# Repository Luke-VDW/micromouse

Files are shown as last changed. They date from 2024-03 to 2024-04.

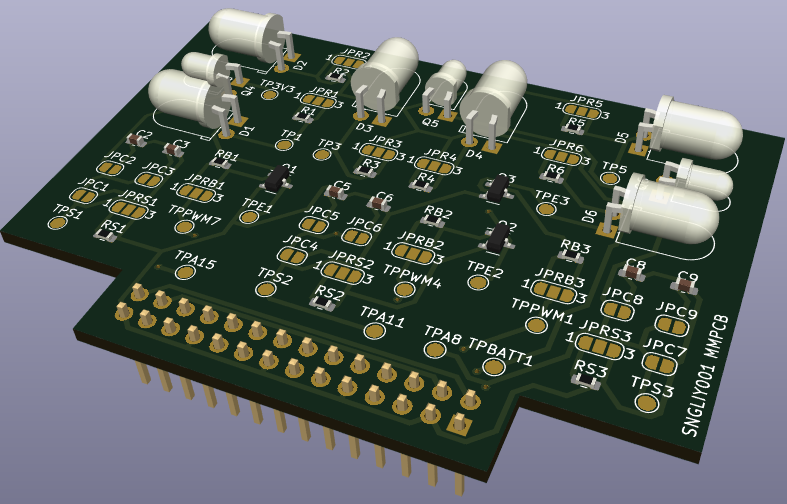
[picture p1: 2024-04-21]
documents/sensing/diagrams/PCB3D.png

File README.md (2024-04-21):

# micromouse
This repository contains all documentation used and deliverables produced for the UCT EEE3088F micromouse project.

A micromouse is a battery powered robot whose goal is to navigate through a maze. The project focuses on the design of the micro-mouse’s hardware. The project is compartmentalised into four subsystems, namely: the motherboard, the processor, power and sensing. The processor subsystem and motherboard subsystem have been completed. This repository will contain the power subsystem and sensing subsystem documentation.

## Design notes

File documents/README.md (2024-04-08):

This folder contains documentation relevant to both the power and sensing subsystem of the micromouse.

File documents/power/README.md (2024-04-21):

This folder contains documentation for the power subsystem within the context of the UCT EEE3088F Micro-mouse project. The power subsystem is one of four subsystems in this project, namely: the motherboard, the processor, power and sensing.

The documentation is for the design and manufacturing of the power subsystem that is responsible for powering the other subsystems.

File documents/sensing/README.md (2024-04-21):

This folder contains documentation for the sensing subsystem within the context of the UCT EEE3088F Micro-mouse project. The sensing subsystem is one of four subsystems in this project, namely: the motherboard, the processor, power and sensing.

The documentation is for the design and development of the sensing PCB responsible for detecting obstructions(walls) nearby and providing the processor with that data.

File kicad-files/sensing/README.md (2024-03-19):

This folder contains all kicad material for the sensing subsystem of the micromouse project.

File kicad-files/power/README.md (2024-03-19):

This folder contains all kicad material for the power subsystem of the micromouse project.

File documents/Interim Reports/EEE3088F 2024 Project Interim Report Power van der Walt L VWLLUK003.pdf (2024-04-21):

# Interim Design Report

Micromouse Power Subsystem


Prepared by:
Luke van der Walt

Prepared for:
EEE3088F
Department of Electrical Engineering University of Cape Town

April 21, 2024

# Declaration

1. I know that plagiarism is wrong. Plagiarism is to use another’s work and pretend that it is one’s own.
2. I have used the IEEE convention for citation and referencing. Each contribution to, and quotation in, this report from the work(s) of other people has been attributed, and has been cited and

referenced.

3. This report is my own work.
4. I have not allowed, and will not allow, anyone to copy my work with the intention of passing it off as their own work or part thereof.

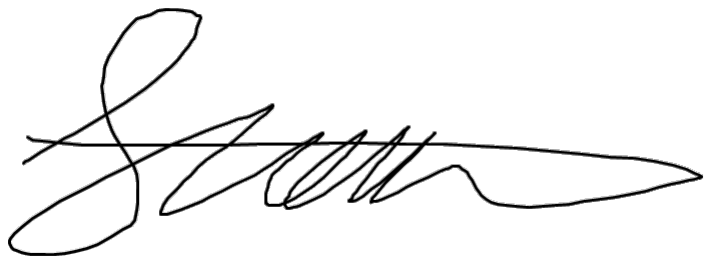
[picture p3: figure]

April 21, 2024

Name Surname | Date

ii

# Contents

1 Introduction | 1
2 Requirements Analysis | 2
3 Subsystem Design | 5
4 Acceptance Testing | 12

iii

# Chapter 1

# Introduction

## 1.1 Problem Description

This project encompasses the development of a power module and it was assigned as part of the EEE3088F course offered by the EBE faculty at the University of Cape Town. It exists under a larger project aimed at developing a micromouse robot. A micromouse is a battery-powered, wheeled robot whose goal is to traverse and solve a maze. In this micromouse project, the robot will navigate through a walled maze structure and attempt to reach its center. The micromouse project is structured around four distinct yet interconnected subsystems namely: the motherboard, processing, power, and sensing subsystems.

This specific project focuses on the power subsystem. The power subsystem needs to provide power from a battery to the motors and it needs to be able to charge the battery. Additionally, it must interface appropriately with the other three subsystems and provide them access to the battery.

## 1.2 Scope and Limitations

This project’s scope covers the design, manufacturing, and hardware testing of the power subsystem for the micromouse project. The developed module only needs to meet the requirements detailed in section 2.1. Note this project does not cover the development of the other three subsystems; this includes any programmed communication or inputs to the power subsystem from other subsystems. Additionally, the physical assembly of this module is done by a third party and lies outside the scope of this project.

This project was limited to a fixed budget of $8.25 and a design completion deadline of 24 March 2024.

Additionally, the design was limited by the following:

- The module with all its components had to be manufactured through JLCPCB.
- The module size and interfacing capabilities were limited by the motherboard subsystem.
- The module could only be tested through simulations or calculations before manufacturing.
- The power supplied was limited to a single 1S1P LiPo battery.

## 1.3 GitHub Link

All relevant information and documentation can be found in the following GitHub repository: https://github.com/Luke-VDW/micromouse/tree/main.

# Chapter 2

# Requirements Analysis

## 2.1 Requirements

The requirements for a micromouse power module are described in Table 2.1.

Table 2.1: User and functional requirements of the power subsystem.

Requirement ID | Description
R01 | Must operate off a single 1S1P LiPo battery
R02 | Must be able to charge the battery from a 5V pin
R03 | Must provide sufficient power to the DC brush motors and other subsystems
R04 | Must enable speed and direction control for the motors
R05 | Must be able to switch the micromouse ON / OFF
R06 | Must charge the battery when the micromouse is off
R07 | Must provide an analogue battery state of charge signal out
R08 | Must cost within the budget
R09 | Must be manufactured with all its components through JLCPCB
R10 | Must fit on a PCB that can connect to the motherboard

## 2.2 Specifications

The specifications, refined from the requirements in Table 2.1, for the micromouse power module are described in Table 2.2.

Table 2.2: Specifications of the power subsystem derived from the requirements in Table 2.1.

Specification ID | Description
SP01 | The battery must connect to the board via a JST PH 2mm connector
SP02 | The module must operate from 3.0 - 4.2V
SP03 | The battery charging input must not exceed 4.2V
SP04 | The battery must be charged at a rate less than 800mA (1C)
SP05 | The motors must each be able to receive up to 200mA of continuous current
SP06 | The module must supply the other subsystems with power at their peak load
SP07 | The motors’ speed and direction must be controlled using 3.3V PWM signals
SP08 | The module must provide 0V or 3.0 - 4.2V to the motors and other subsystems
SP09 | When the micromouse is OFF the battery must draw below 500uA
SP10 | When the micromouse is OFF the charging circuitry must still connect to the battery
SP11 | The SoC output must be less than 3.3V
SP12 | The module must cost less than $8.25
SP13 | The components chosen for the module must be sufficiently stocked at JLCPCB
SP14 | The board must be smaller than 100x100mm
SP15 | Must have a 2x8 2.54mm pin pitch header to connect to the motherboard
SP16 | The header must be centred in a tab with a minimum height of 18mm and a maximum width of 35mm

2.3. Testing Procedures

## 2.3 Testing Procedures

A summary of the testing procedures detailed in chapter 4 is given in Table 2.3.

Table 2.3: Testing procedures of the power subsystem derived from the specifications in Table 2.2

Acceptance Test ID | Description
AT01 | Check the module turns on
AT02 | Measure the input battery voltage
AT03 | Measure battery input current
AT04 | Measure the current going into the motors
AT05 | Measure the current going to the other subsystems
AT06 | Measure the frequency and direction of the motor output voltage
AT07 | Measure the voltage output to the motors and subsystems when switched off
AT08 | Measure the current going to the entire micromouse
AT09 | Measure the SoC voltage output
AT10 | Use JLCPCB to check prices and stock levels
AT11 | Measure the module’s physical dimensions
AT12 | Check the module can connect to the motherboard using the header

## 2.4 Traceability Analysis

The show how the requirements, specifications and testing procedures all link, Table 2.4 is provided.

Table 2.4: Requirements Traceability Matrix

# | Requirements | Specifications | Acceptance Test

1 2 3 4 5 6 7 8 9 10 | R01 R02 R03 R04 R05 R06 R07 R08 R09 R10 | SP01,SP02 SP03,SP04 SP05,SP06 SP07 SP08,SP09 SP10 SP11 SP12 SP13 SP14,SP15,SP16 | AT01 AT02,AT03 AT04,AT05 AT06 AT07,AT08 AT02,AT03,AT07 AT09 AT10 AT10 AT11,AT12

### 2.4.1 Traceability Analysis 1

From R01, SP01 and SP02 can be deduced because the battery being used has a JST PH 2mm connector, and the module must operate at the supplied battery voltage which ranges from 3.0V -4.2V. This can be tested with AT01 to see if the module turns on.

### 2.4.2 Traceability Analysis 2

From R02, SP03 and SP04 can be deduced because the battery has a maximum voltage of 4.2V and a maximum rated charge current of 800mA (1C). These can be tested with AT02 and AT03 by measuring

the voltage across and the current flowing into the battery.

2.4. Traceability Analysis

### 2.4.3 Traceability Analysis 3

From R03, SP05 and SP06 can be deduced because the module should allow the motor to operate at the maximum current they can draw at the rated voltage of the battery, which is 200mA. The module should also be capable of transferring power to the other subsystems at their peak loads. This can be tested with AT04 and AT05 to check that the module can transfer enough power.

### 2.4.4 Traceability Analysis 4

From R04, SP07 can be deduced because the module only has access to 2 PWM signals for motor control and these come from the STM32 processor which outputs 3.3V logic signals. This can be tested with AT06 to ensure that the module will output the correct response from a set of PWM inputs.

### 2.4.5 Traceability Analysis 5

From R05, SP08 and SP09 can be deduced because when the micromouse is considered switched off the output voltage from the module must be 0V the battery current must be below 500uA; when switched on the output voltage must be between 3.0-4.2V and adhere to SP05. This can be tested with AT07 and AT08 by measuring the output voltage and battery current when it is switched on or off.

### 2.4.6 Traceability Analysis 6

From R06, SP10 can be deduced because the charging circuit must always be connected to the battery so it can charge when the micromouse is switched off. This can be tested with AT02, AT03 and AT07 to check that at 0V output voltage, the battery is charging at its rated values.

### 2.4.7 Traceability Analysis 7

From R07, SP11 can be deduced because the output of the analogue battery state of charge signal goes to an ADC input on the STM32L4 processor, which has a maximum rated reading input voltage of 3.3V. This can be tested with AT09 to ensure it is below 3.3V.

### 2.4.8 Traceability Analysis 8

From R08, SP12 can be deduced because this project has a budget of $8.25. This can be tested with

AT10 to check the total board price.

### 2.4.9 Traceability Analysis 9

From R09, SP13 can be deduced because all manufacturing done and components used in this project are limited to what is offered on JLCPCB. This can be tested with AT10 to check that the components used are available at JLCPCB.

### 2.4.10 Traceability Analysis 10

From R10, SP14, SP15, and SP16 can be deduced because the module must be able to connect with the motherboard through a 2x18 pin connector and because the size of the module is limited by the motherboard. This can be tested with AT11 and AT12 to check that the board fits onto the motherboard.

# Chapter 3

# Subsystem Design

## 3.1 Design Decisions

The power module was broken up into 4 main sections for the sake of the design decisions. These sections are the charging, driver, SoC and PCB design sections as seen in Figure 3.1.

Figure 3.1: Section diagram for the power module

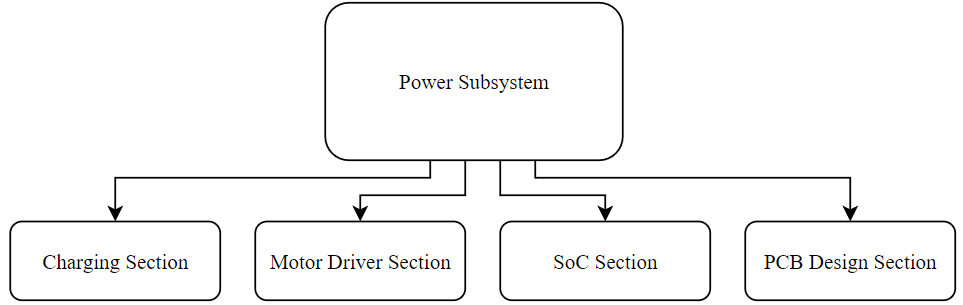
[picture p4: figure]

### 3.1.1 Charging Section

The charging section for the battery must meet requirements: R02, R06, R08 and R09 listed in Table 2.1. Therefore the circuit must comply with specifications: SP03, SP04, SP09, SP10, SP12, and SP13 listed in Table 2.2.

Considerations to take into account when meeting the requirements include:

- The solution should be very reliable since improperly charging the battery is a fire hazard
- The solution should draw below 500uA when it is not charging because it will remain connected to the micromouse when it is switched off
- The battery charging current should be optional to allow for different charging currents
- The battery should not take excessively long to charge

Possible design solutions can be seen in Table 3.1.

Table 3.1: Possible design solutions for the charging section

Design Solution ID | Possible Design Solution
DS01 | Use a custom charging circuit with auto-cutoff and current limiting
DS02 | Use a LiPo charging IC available

Chosen solution: DS02

A custom charging circuit would provide and more modifiable circuit than using an IC however it is much more complicated and is less safe than a dedicated LiPo charging IC. Additionally, a charging IC will likely be more efficient than a custom circuit and come with documentation to support all its parameters, hence it is the preferred solution.

Some available battery management ICs that satisfy the charging requirements can be seen in Table 3.2 below:

3.1. Design Decisions

Table 3.2: Component considerations for the charging section

Component | Price ($) | Stock | Basic part | Adjustable current | Max current (A)
TP4056-42 | 0.1724 | 107303 | Yes | Yes | 1
GX4057 | 0.0189 | 14048 | Yes | No | 0.5
TP4057-42 | 0.1163 | 21877 | Yes | Yes | 0.5

Chosen component: TP4056-42 (https://dlnmh9ip6v2uc.cloudfront.net/datasheets/Prototyping/TP4056.pdf)

The GX4057 is much cheaper than the other options, however since it is not a basic part it will have an extended component fee of $2.87 and hence is significantly more expensive than the other options.

The TP4057-42 is cheaper than the TP4056-42 however its charging current is limited to 500mA and it is less available, which makes the TP4056-42 the preferred component.

Calculations for the TP4056-42:

The charging current is given as IBAT =

| | | 1 RP ROG
× 1200 where RP ROG is a resistor connected to the PROG pin (pin 2) and ground.

The maximum charging current for the battery is 800mA and the recommended is 400mA. Any charging current between these values will be fast enough and safe. The associate resistor values are:

| 0.8 = | 1

RP ROGmax

| | | × 1200 | ∴ RP ROGmax = 3kΩ
| 0.4 = | 1

RP ROGrec

| | | × 1200 | ∴ RP ROGrec = 1.5kΩ

The STDBY and CHRG pins (pins 6 and 7) can be connected to a green and red LED respectively.

These are used to indicate when the unit is charging. A 1kΩ resistor can be placed in series with the LED to limit the current through them.

As recommended by the datasheet a 10µF capacitor can be connected across VCC and ground and across the BAT pin and ground. Additionally, a limiting resistor should be connected in series with VCC that can range between 0.2Ω - 0.5Ω. The max power that could be dissipated across this resistor is P = I

2 × R = 0.8

2 × 0.5 = 0.32W. Therefore use two or more 250mW 1Ω resistors in parallel to

achieve this limiting resistance.

### 3.1.2 Motor Driver Section

The motor driver section must meet requirements: R01, R03, R04, R08 and R09 listed in Table 2.1. Therefore the circuit must comply with specifications: SP02, SP05, SP07, SP08, SP12 and SP13 listed in Table 2.2.

Considerations to take into account when meeting the requirements include:

- The solution should be capable of running at high PWM frequencies to provide a broad range for user selection

3.1. Design Decisions
- The output impedance for the incoming PWM signals should be kept high since this signal is a logic signal coming from the processor and is not meant to deliver power
- If a motor is connected across the battery directly, its voltage will decrease over time which will affect the motor’s speed

Possible design solutions can be seen in Table 3.3:

Table 3.3: Possible design solutions for the charging section

Design Solution ID | Possible Design Solution
DS03A | Use a custom H-bridge circuit powered directly from the battery
DS03B | Use a custom H-bridge circuit powered by a regulated voltage
DS04A | Use a motor driver IC powered directly from the battery
DS04B | Use a motor driver IC powered by a regulated voltage

Chosen solution: DS04A

A custom H-bridge circuit would provide a more modifiable circuit than using an IC however it is much more complicated and could potentially be less reliable than a driver IC. Operating at a constant voltage would provide stability on the output but it would also require a voltage regulator which would decrease the overall efficiency. The loss in efficiency is more important than the improved stability since the output can be controlled with a PWM input, which can be used to compensate for the changing battery voltage, and hence solution DS04A is the preferred solution.

Some available motor driver ICs that satisfy the motor driver requirements can be seen in Table 3.4:

Table 3.4: Component considerations for the charging section

Component | Price ($) Stock | Basic
part

No. of
drivers

Max
current (A)

Operating
voltage (V)
DRV8833PWPR | 0.6660 | 9436 | No | 2 | 1.5 | 2.7 - 10.8
DRV8837DSGR | 0.1235 | 71521 | No | 1 | 1.8 | 1.8 - 7.0

Chosen component: DRV8833PWPR (https://wmsc.lcsc.com/wmsc/upload/file/pdf/v2/lcsc/1810151712_Texas-Instruments-DRV8833PWPR_C50506.pdf)

The DRV8837DSGR and the DRV8833PWPR can both meet the requirements for the driver circuit, however, the DRV8833PWPR is a dual driver and can therefore operate both motors at the same time. Having one IC instead of two reduces the complexity of the module which is favoured over the small cost difference between the two and therefore the DRV8833PWPR is the preferred component.

Calculations for the DRV8833PWPR:

As recommended by the datasheet a 10µF ceramic capacitor can be connected across VM and ground and a 2.2µF ceramic capacitor can be connected across VINT and ground. Additionally, a 10nF ceramic capacitor can be connected across VM and VCP. AISEN and BISEN can be grounded to ignore current limits.

3.1. Design Decisions

### 3.1.3 SoC Section

The SoC section must meet requirements: R01, R07, R08 and R09 listed in Table 2.1. Therefore the circuit must comply with specifications: SP02, SP11, SP12, and SP13 listed in Table 2.2.

Considerations to take into account when meeting the requirements include:

- The voltage output should be a linearly scaled version of the input since this output signal will be used to determine the battery state of charge
- The output must be able to be polled by an ADC input without unwanted loading effects

Possible design solutions can be seen in Table 3.5.

Table 3.5: Possible design solutions for the SoC section

Design Solution ID | Possible Design Solution
DS05 | Use a voltage diver to scale the input and then output from an op-amp buffer
DS06 | Use a voltage diver to scale the input and then output after a capacitor acting as a buffer

Chosen solution: DS06

The op-amp buffer would be reliable and easy to implement however since we are operating at low voltages it would be easier to avoid using active components that can run into headroom issues. Therefore, since it is a passive solution, DS06 is the preferred solution.

Calculations for the SoC section:

The voltage divider input ranges from 3.0 - 4.2V. The output must be below 3.3V for the ADC to be able to properly read it therefore, so for the maximum VIN :

VOUT = VIN ×

R2
R1 + R2

∴ 3.3 = 4.2 ×

R2
R1 + R2

∴ R1 = R2 × 0.273

LetR2 = 10kΩ ∴ R1 = 2.73kΩ

Let R1 be a larger E24 value to ensure that the voltage is always lower than 3.3V, i.e. R1 = 3kΩ:

∴ VOUTmax = 4.2 ×

10k
3k + 10k

= 3.23V

The buffer capacitor for the output can be any size that is larger than the internal capacitor on the ADC of the processor.

3.1. Design Decisions

### 3.1.4 PCB Design Section

The PCB section must meet requirements: R03, R05, R08, R09 and R10 listed in Table 2.1. Therefore the circuit must comply with specifications: SP01, SP06, SP08, SP12, SP13, SP14, SP15 and SP16 listed in Table 2.2.

Considerations to take into account when meeting the requirements include:

- The switch should hold its position (latching) and should handle the peak current draw
- The PCB power traces should be able to handle the peak current draw of the micromouse
- The PCB should be as short as possible to help maintain a central centre of mass
- Power components should be as close together as possible to reduce the length of power traces

### 3.1.5 Final Design

The following design was chosen based on the design solutions DS02, DS04A and DS06 and any accompanying design considerations for each section above. The solution makes use of the TP4056-42 and the DRV8833PWPR as ICs for the charging and motor driver sections. For the charging circuit, five 1Ω are placed in parallel with jumpers to provide optional resistance values for the limiter resistor. Also, a parallel resistor loop controlled by a switch is connected alongside RP ROG to toggle the charging speed of the battery. The SoC section was designed with a range of buffer capacitor options. A large toggle switch was chosen to switch the micromouse on and off easily.

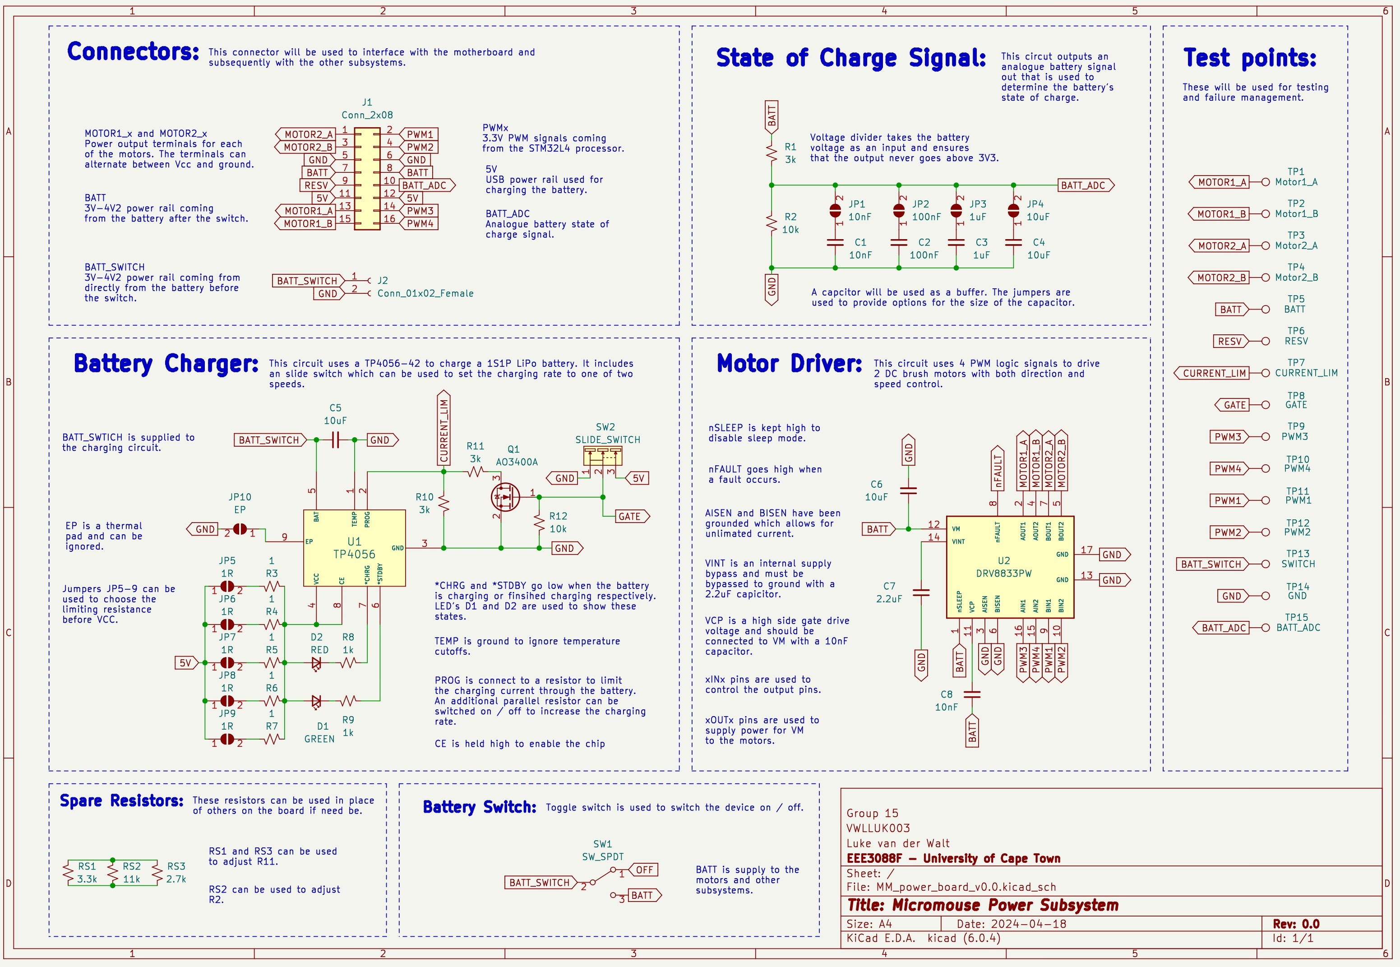
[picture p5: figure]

Figure 3.2: Final Schematic

3.2. Failure Management

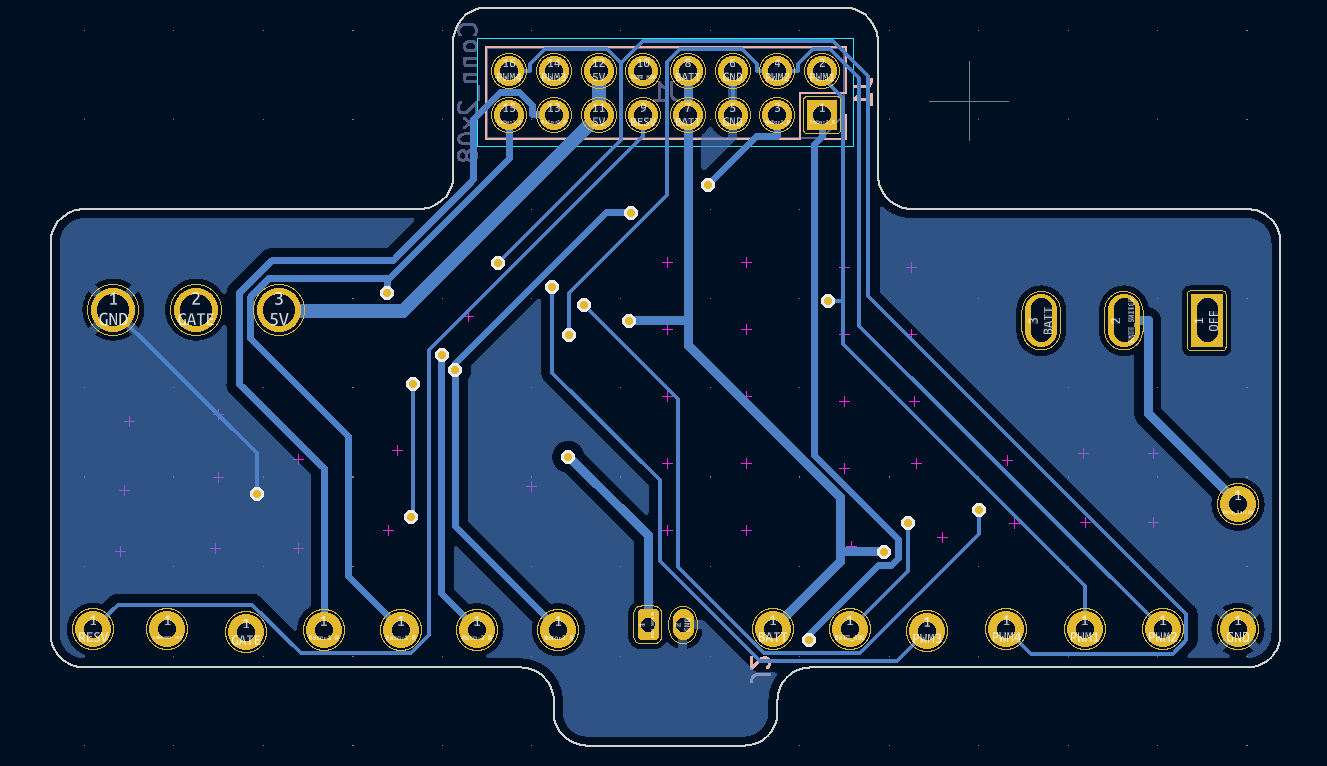
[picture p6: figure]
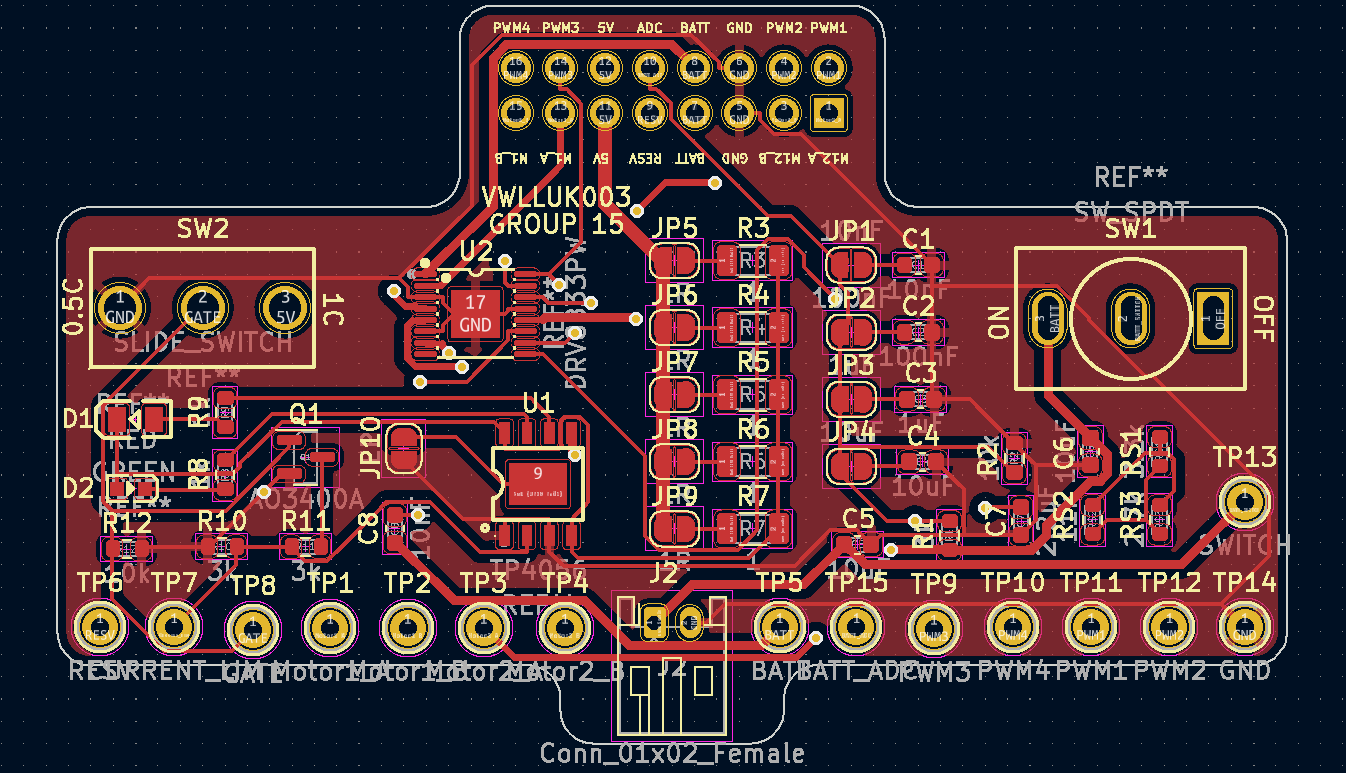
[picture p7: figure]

(a) Front PCB | (b) Back PCB

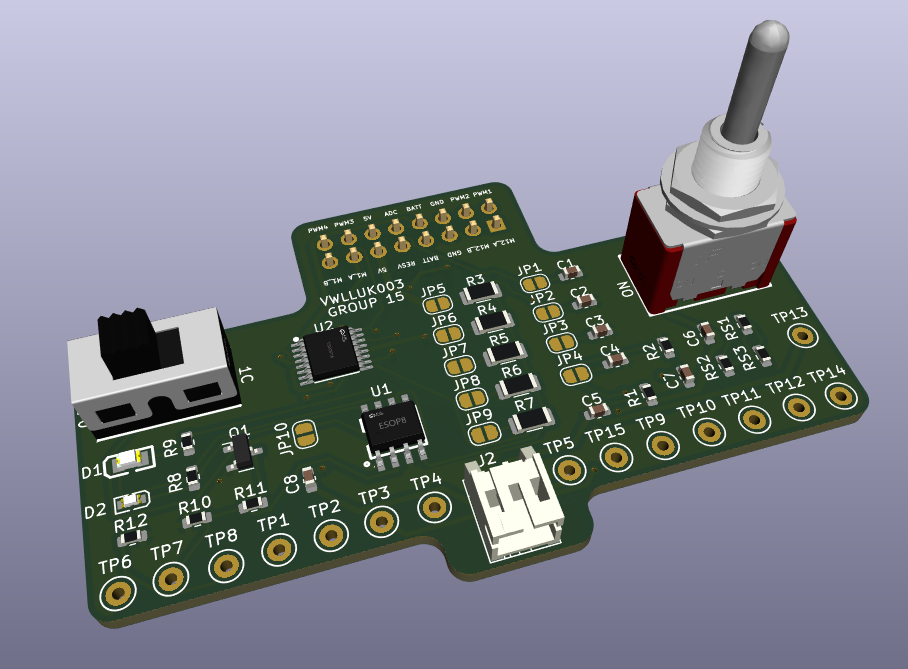
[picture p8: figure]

(c) 3D PCB

Figure 3.3: PCB

## 3.2 Failure Management

The steps taken to manage potential errors are detailed in Table 3.6.

Table 3.6: Failure management processes

Name | Description
Spare components | Spare resistors were added to the board. These resistors can be removed and placed elsewhere on the board if any other resistor values are off.
Jumpers | Jumpers have been placed in areas where the value of a component is uncertain to provide multiple options for that component.
TH test points | All test points are keystone / through hole which provides space to connect additional components in the event of a component failure.
Power test points | All power test points in the circuit have been connected using the same thick traces that the dedicated power lines use. This allows for power to be provided from these test points to other components through external connections if their traces have been incorrectly run.
Variable charging speed | A switch has been added to the charging circuit that allows for two different charging rates. If the set charging rate is too slow, this can be used to increase the charging rate, or it can be ignored if the rate is satisfactory.

3.3. System Integration and Interfacing

## 3.3 System Integration and Interfacing

Table 3.7: Interfacing specifications

Interface | Description | Pins/Output

PWM signals from STM
to power module through
header J1
- PWM1: STM PC6 to header PIN 2
- PWM2: STM PC7 to header PIN 4
- PWM3: STM PC8 to header PIN 14
- PWM4: STM PC9 to header PIN 16

Power from power module
to motors through header
J1
- MOTOR1_A: Header PIN 13 to Motor1 PIN A
- MOTOR1_B: Header PIN 15 to Motor1 PIN B
- MOTOR2_A: Header PIN 1 to Motor2 PIN A
- MOTOR2_B: Header PIN 3 to Motor2 PIN B
IJ1 | 3V - 4.2V power from the
power module to other subsystems through header J1
- BATT: Header PIN 7 and PIN 8 to STM VBAT
- GND: Header PIN 5 and PIN 6 to STM GND

5V power from USB to
power | module | through
header J1
- 5V: USB to header PIN 11 and PIN 12

Analogue SoC signal from
power module to STM
through header J1
- BATT_ADC: Header PIN 10 to STM 3V3 ADC
IJ2 | 3V - 4.2V power from battery to power module through JST connect J2
- BATT_SWITCH: + terminal to JST PIN 1
- GND: - terminal to JST PIN 2

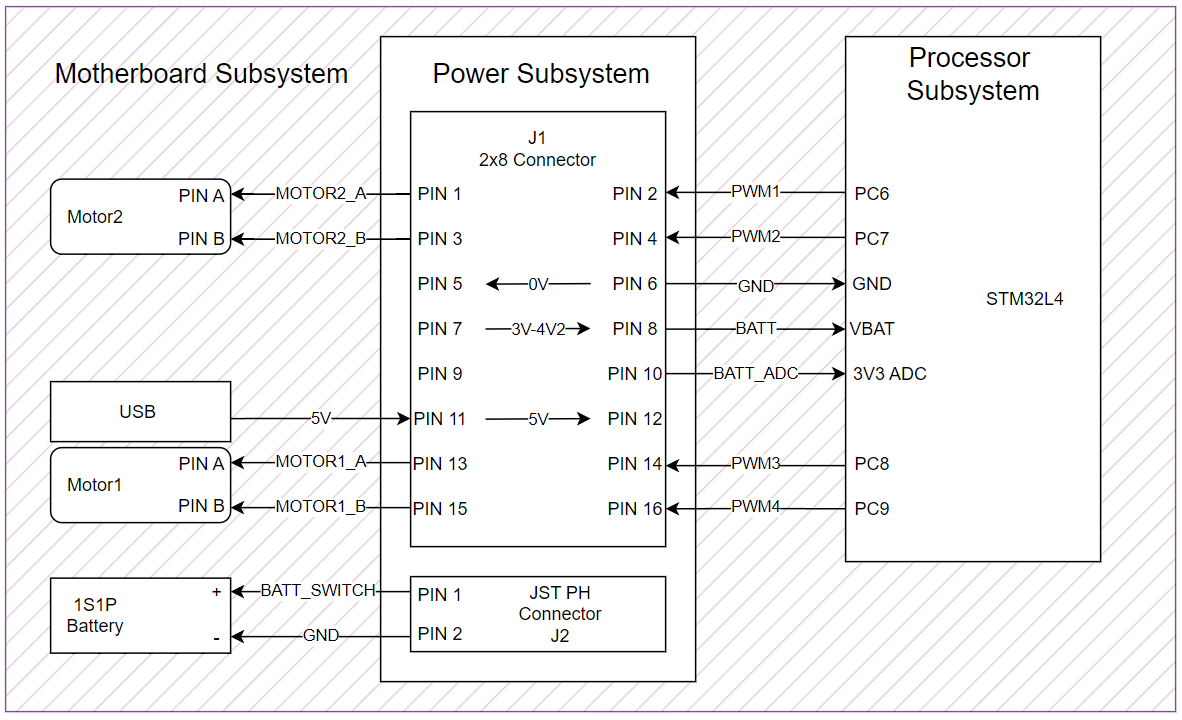
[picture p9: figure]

Figure 3.4: Interfacing Diagram

# Chapter 4

# Acceptance Testing

## 4.1 Tests

Table 4.1: Subsystem acceptance tests

Test
ID | Description | Testing Procedure | Pass Criteria
AT01 | Check the module
| turns on | • Connect the battery to the JST connector
| | • Measure the voltage on the PIN12 (VM) of U2 | 3V - 4V2
AT02 | Measure the input
| battery voltage | • Power the 5V pins on J1
| | • Measure the voltage across the terminals of J2
| | which is VBAT in | VBAT in ≈ 4V 2
AT03 | Measure battery input current
- Connect the positive terminal of an ammeter to
TP13 (BATT_SWITCH)
- Connect a semi-charged battery across the negative ammeter terminal and TP14 (GND)
- Power the 5V pins on J1
- Record IBAT T

IBAT T ≥ 0.4A
IBAT T ≤ 0.8A

AT04 Measure the cur- rent going into the motors
- Connect the positive terminal of an ammeter to TP1 (MOTOR1_A)
- Connect the negative terminal of the ammeter to pin A of Motor1 and PIN15 of J1 to pin B
- Connect a battery charged at 4V2
- apply a 3.3V DC signal to TP9 (PWM3) and connect TP10 (PWM4) to ground
- Repeat this for motors and record IM

IM > 0A
IM ≤ 0A2

AT05 Measure the cur- rent going to the other subsystemsConnect the positive terminal of an ammeter to TP5 (BATT)
- Connect the negative ammeter terminal to the BATT pin on the motherboard header
- Connect TP14 (GND) to the GND pin on the motherboard header
- Connect a charged battery to J2
•
- Record ISUB

ISUB ≤ 0A8

AT06 Measure the fre- quency and direc- tion of the motor output voltage

- Connect an oscilloscope to TP1 (MOTOR1_A)
- Record the fOUT and |VOUT |
- Repeat for TP3 (MOTOR2_A)

fOUT = fIN

Vout = Vbatt

4.1. Tests
AT07 | Measure | the
voltage output to
the motors and
subsystems when
| switched off
- Measure the voltage on TP5 (BATT)
- Record VBAT T

VBAT T = 0V

AT08 • Measure the cur- rent going to the entire micromouseConnect the positive terminal of an ammeter to TP13 (BATT_SWITCH)
- Connect a charged battery across the negative ammeter terminal and TP14 (GND)
- Connect header J1 to the motherboard
- Record Imm

Imm ≤ 0A8

AT09 Measure the SoC voltage output

- Measure the voltage on TP15 (BATT_ADC)
- Record VADC

VADC ≤ 3V 3

AT10 Use JLCPCB to check prices and stock levels taking
- Take note of basic vs extended parts
- Make a quote using the bill of materials and determine the total cost of the board
- Record Cost

Cost ≤ 8.25$

AT11 Measure the mod- ule’s physical di- mensions
- Use a measuring tool to measure the board’s total area A
- Use a measuring tool to measure the tab height

Htab
- Use a measuring tool to measure the tab width

Hwid

A ≤ 10 × 10cm
Htab ≥ 18mm
Hwid ≤ 35mm

AT12 Check the module can connect to
the motherboard
using the header
- Try to place the module header into the motherboard connector
- Once placed check that the module has access to the battery connector

Fits wihtout
obstruction

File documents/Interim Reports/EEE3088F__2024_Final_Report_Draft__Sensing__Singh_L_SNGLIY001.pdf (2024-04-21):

# Interim Design Report

Micromouse Sensing Subsystem


Prepared by:
Liyana Singh
SNGLIY001

Prepared for:
EEE3088F
Department of Electrical Engineering University of Cape Town

April 21, 2024

# Declaration

1. I know that plagiarism is wrong. Plagiarism is to use another’s work and pretend that it is one’s own.
2. I have used the IEEE convention for citation and referencing. Each contribution to, and quotation in, this report from the work(s) of other people has been attributed, and has been cited and referenced.
3. This report is my own work.
4. I have not allowed, and will not allow, anyone to copy my work with the intention of passing it off as their own work or part thereof.

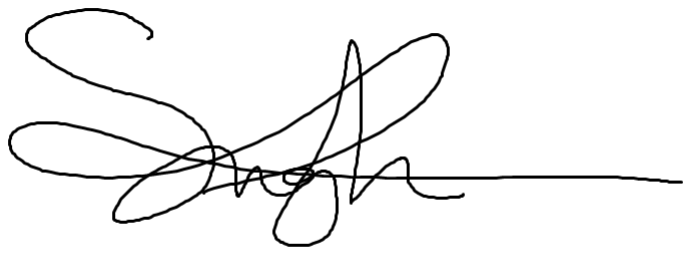
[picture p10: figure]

April 21, 2024

Name Surname | Date

ii

# Contents

1 Introduction | 1
2 Requirements Analysis | 2
3 Subsystem Design | 5
4 Acceptance Testing | 12

iii

# Chapter 1

# Introduction

### 1.1 Problem Description

### 1.1.1 Design Problem Statement

Design and develop a sensing PCB responsible for detecting obstructions(walls) nearby and providing the processor with that data.

### 1.1.2 Context

A micro-mouse is a battery powered robot whose goal is to navigate through a maze. This report is written on the sensing subsystem within the context of the UCT EEE3088F Micro-mouse project. The project focuses on the design of the micro-mouse’s hardware. The sensing subsystem is one of four subsystems in this project, namely: the motherboard, the processor, power and sensing.

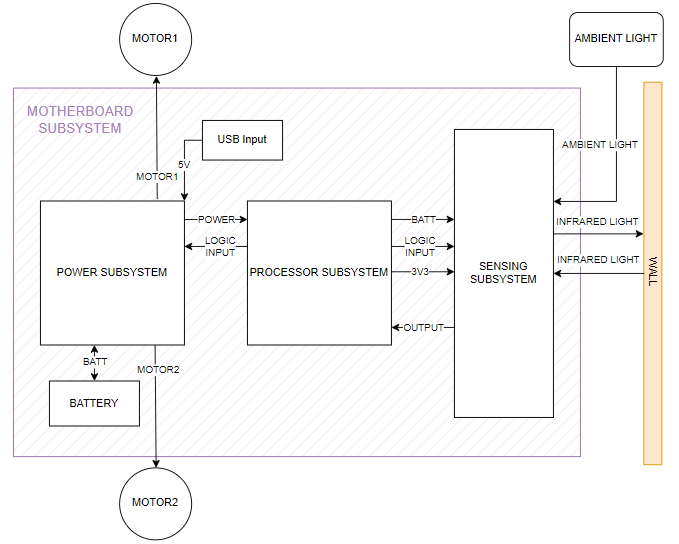
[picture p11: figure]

The motherboard connects all the subsystems. It
acts as a baseboard that the sensing subsystem slots
onto to connect to the processor subsystem. The power subsystem supplies the motherboard with power. The sensing subsystem is connected to the battery and 3.3V supply via the processor. The processor also supplies a logic input to the sensing subsystem. The sensing subsystem interacts with the environment to detect walls in the way of the micro-mouse. The sensing subsystem sends this data to the processor to be interpreted. This is summarised in Figure 1.1 adjacent. The power subsystem has been added for completeness but can be ignored.

Figure 1.1: Context Diagram

### 1.2 Scope and Limitations

The scope includes the design of the sensing PCB but the manufacturing of the PCB is external. It must detect walls, however, it does not have to interpret any data. The data is sent to the processor to be interpreted. It has design limitations: it must fit onto the pin headers on the motherboard, it must be an appropriate size for the micro-mouse and the components must be available on JLCPCB. Additionally, it has financial limitations: must not exceed $16.5 for two boards. Finally, it has a time limitation: must be completed by May 17th 2024.

### 1.3 GitHub Link

https://github.com/Luke-VDW/micromouse

# Chapter 2

# Requirements Analysis

### 2.1 Requirements

The requirements for a micro-mouse sensing module are described in Table 2.1.

Table 2.1: Requirements of the Sensing Subsystem.

Requirement ID | Description
R01 | It must be externally powered.
R02 | It must not exceed the power and current limitations.
R03 | It must detect walls.
R04 | It must prove it can detect walls
R05 | It must fit onto the pin headers on the motherboard.
R06 | It must be an appropriate size for the micro-mouse.
R07 | It must adhere to the budget.
R08 | All components must come from JLCPCB .

### 2.2 Specifications

The specifications, refined from the requirements in Table 2.1, for the micro-mouse sensing module are described in Table 2.2.

Table 2.2: Specifications of the Sensing Subsystem

Specification ID | Description
S01 | The IR emitter circuitry voltage will be supplied by the Battery LiPo 800mAh 3.7V.
S02 | The IR sensor circuitry voltage will be supplied by the 3.3V supply from the processor.
S03 | The maximum draw of 400mA from the battery results in a discharge time from full to fully discharged of 2 hours.
S04 | It must detect walls at the front, left and right sides of the PCB.
S05 | A simple code must be written to interpret the sensing subsystem’s output voltage that is sent to the processor.
S06 | The output voltage should be significantly greater than the minimum voltage output to indicate detection. The sensor detects ambient light and therefore the output voltage will have a non-zero minimum voltage output.
S07 | It must have a pin pitch less than or equal to 2.54mm.
S08 | The PCB’s size must not exceed an 80mm square.
S09 | The PCB component cost must not exceed $16.5 for 2 boards.
S10 | JLCPCB must have more than 1000 units available of the component.

2.3. Testing Procedures

### 2.3 Testing Procedures

A summary of the testing procedures detailed in chapter 4 is given in Table 2.3.

Table 2.3: Summary of Testing Procedures

Acceptance Test ID | Description
AT01 | Measure voltage across IR emitter circuitry.
AT02 | Measure voltage across IR sensor circuitry.
AT03 | Measure the current through the IR emitter circuit.
AT04 | Measure the current through the IR sensor circuit.
AT05 | Check there is IR emitter circuitry and IR sensor circuitry for the front, left and right sides of the PCB.
AT06 | The processor board has three LEDs. Observe LED1, LED2 and LED3 which indicate a wall is sensed on the left, front and right, respectively, by turning on. If no wall is sensed, then no LEDs will be on.
AT07 | Measure the output voltage of the IR sensor circuitry.
AT08 | Measure the pin pitch on the sensing PCB.
AT09 | Measure the PCB’s length and width.
AT10 | Check PCB cost is within budget.
AT11 | Check the manufacturing bill of materials.

### 2.4 Traceability Analysis

Table 2.4 shows how the requirements, specifications and testing procedures all link.

Table 2.4: Requirements Traceability Matrix

# | Requirements | Specifications | Acceptance Tests

1 | R01 | S01 S02 | AT01 AT02
2 | R02 | S03 | AT03 AT04
3 | R03 | S04 | AT05
4 | R04 | S05 S06 | AT06 AT07
5 | R05 | S06 | AT08
6 | R06 | S07 | AT09
7 | R07 | S08 | AT10
8 | R08 | S09 | AT11

### 2.4.1 Traceability Analysis 1

The sensing subsystem must be externally powered (R01). The voltage across the IR emitter circuitry (S01) will be measured (AT01) to test whether the voltage is within the battery’s range. Therefore, indicating whether it is successfully powered by the battery. The voltage across the IR sensor circuitry (S02) will be measured (AT02) to test whether the voltage is approximately 3.3V. Therefore, indicating whether it is successfully powered by the processor output.

2.4. Traceability Analysis

### 2.4.2 Traceability Analysis 2

The sensing subsystem must not exceed the power and current limitations(R02). The current through the IR emitter circuitry (AT03) and the IR sensing circuitry (AT04) will be measured to test whether they exceed the 400mA total current limit (S03).

### 2.4.3 Traceability Analysis 3

The sensing subsystem must detect walls (R03) at the front, left and right sides of the PCB (S04). Therefore, a check for IR emitter circuitry and IR sensor circuitry for the front, left and right sides of the PCB (AT05) is performed.

### 2.4.4 Traceability Analysis 4

The sensing subsystem must be able to prove it can detect walls (R04). A simple code must be written to interpret the sensing subsystem’s output voltage that is sent to the processor (S05) which has three LEDs. Observing whether LED1, LED2 and LED3 are on or off (AT06) is effective in proving detection. The detection can also be determined directly by measuring the output voltage of the IR sensor circuitry (AT07). The output voltage should be significantly greater than the minimum voltage output, due to ambient light, to indicate detection (S06).

### 2.4.5 Traceability Analysis 5

The sensing PCB must fit onto the pin headers on the motherboard (R05). Measure the pin pitch on the sensing PCB (AT08) to determine whether they exceed the 2.54mm maximum pin pitch limit (S07).

### 2.4.6 Traceability Analysis 6

The sensing PCB must be proportional to the micro-mouse (R06). The length and width of the PCB must be measured (AT09) to determine whether they are less than 80mm (S08). Thus indicating correct or incorrect proportionality.

### 2.4.7 Traceability Analysis 7

The sensing PCBs must adhere to the budget (R07). The budget for 2 boards is $16.5 (S09). This will be checked (AT10) to ensure the PCBs cost has not exceeded the budget.

### 2.4.8 Traceability Analysis 8

Components are limited to availability at JLCPCB (R08). To ensure the component is added to the PCB, JLC must have more than 1000 units available of the component (S10). This will be checked (AT11) to ensure the PCB will be populated with the components ordered.

# Chapter 3

# Subsystem Design

### 3.1 Design Decisions

The sensing subsystem has four major design elements. The IR emitter and IR sensor circuitry, the power supply, the logic addition and The PCB shape. The design options are evaluated and compared in Table 3.1, Table 3.2, Table 3.4 and Table 3.3, respectively. Finally, a design decision is made and the other designs are discarded.

### 3.1.1 IR Emitter and IR Sensor Circuitry

Table 3.1: IR Emitter and IR Sensor Circuitry Options

| Option | Pro | Con
1 | The IR emitting diode and the photo-transistor are mounted side by side as one component. | The photo-transistor only detects the emitted IR light after it has been reflected. It does not detect the IR light directly because there is a divider between the emitting diode and the photo-transistor. | Only one IR emitting diode per photo-transistor limits the proximity at which the photo-transistor can detect walls.
2 | The IR emitting diode and the photo-transistor individual com-ponents. | Many IR emitting diodes per photo-transistor which increases the proximity at which the photo-transistor can detect walls. | The photo-transistor detects IR light emitted directly from the diode because there is no divider between the emit-ting diode and the photo-transistor. The photo-transistor detects the reflected IR light and the direct IR light. The photo-transistor will therefore have inaccurate proximity sensing.

Design decision: Option 2
Three photo-transistors will be used at the left, front and right sides of the PCB. Each photo-transistor will have two IR emitting diodes on either side which will increase the proximity at which the photo-transistor can detect walls. To combat the direct IR light detected by the photo-transistor, a divider (black insulation tape) can be inserted between the IR emitting diodes and photo-transistors after the PCB has been manufactured and delivered.

Note discarded design:
Option 1 could be chosen. To combat the issue of having only one IR emitting diode per photo-transistor, additional individual IR emitting diodes can be added. However, the addition of another extended components will cause budget issues. Additionally, the availability of the integrated photo-transistor and IR emitting diode components are limited. This would have caused issues during component selection subsection 3.1.5.

3.1. Design Decisions

### 3.1.2 Power Supply

Table 3.2: Power Supply Options

| Option | Pro | Con
1 | Battery LiPo 800mAh 3.7V | A maximum of 400mA current can be drawn. A large amount of current through the diodes cause the diodes to emit a large amount of IR light. This in-creases the proximity at which the photo-transistor can detect walls. | The battery voltage is unstable. This causes unpredictable voltage outputs from the senor circuitry to the processor. The processor cannot accurately interpret the data.
2 | STM32L476 3V3 Output | 3V3 voltage is stable. Therefore, there is predictable voltage outputs from the senor circuitry to the processor. The pro-cessor accurately interpret the data. | A maximum of 100mA current can be drawn from the I/O pins. A small amount of current through the diodes cause the diodes to emit a small amount of IR light. This decreases the proximity at which the photo-transistor can detect walls.

Design decision: Option 1 and Option 2
The Battery LiPo 800mAh 3.7V powers the IR emitter circuitry. This ensures enough current is supplied to the diodes to increase IR emitted light which increases the proximity at which the photo-transistor can detect walls. The STM32L476 3V3 Output powers the IR sensor circuitry. This ensures the voltage supply is stable and therefore there is predictable voltage outputs from the senor circuitry to the processor.

Note discarded design:
Powering the sensing subsystem with only the Battery LiPo 800mAh 3.7V or only the STM32L476 3V3 Output will have either current or voltage issues. Both issues cause serious operational defects as discussed in Table 3.2.

### 3.1.3 PCB Shape

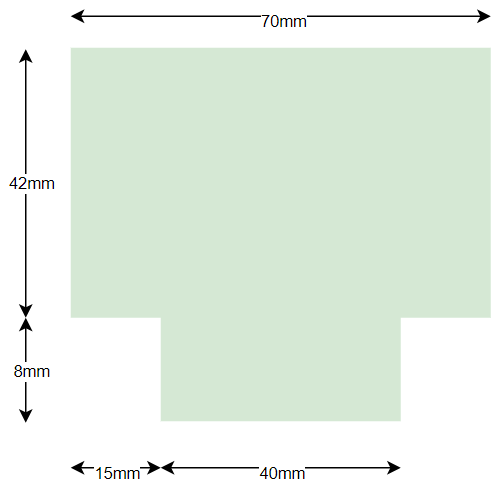
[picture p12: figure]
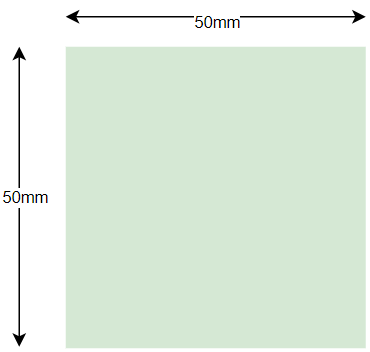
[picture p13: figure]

Figure 3.1: PCB Shape Small | Figure 3.2: PCB Shape Wide

3.1. Design Decisions

Table 3.3: PCB Shape Options

| Option | Pro | Con
1 | A small square 50mmx50mm PCB seen in Figure 3.1. | The micro-mouse will have a smaller turn-ing circle for ease of navigation through the maze. | The maze is 200mm wide. The IR emit-ting diodes will be approximately 75mm from the left and right side walls of the maze. The walls may be out of the photo-transistor’s range.
2 | A wide ’T’ shape 50mmx70mm PCB seen in Figure 3.2. | The maze is 200mm wide. The IR emit-ting diodes will be approximately 65mm from the left and right side walls of the maze. The walls will be within the photo-transistor’s range. | The micro-mouse’s larger turning circle will impede its ability to navigate through the maze efficiently.

Design decision: Option 2
The walls must be within range of the photo-transistor for the sensing subsystem to meet it’s requirements. The turning circle will hinder the micro-mouses ability to efficiently navigate the maze but it will still be functional. It is less than a 80mm square to meet the specification.

Note discarded design:
Option 1 could have been chosen. It is less than a 80mm square to meet the specification. The micro-mouse would be able to efficiently solve the maze provided the photo-transistor can detect the walls. However, if the photo-transistor cannot detect the walls, it will not be functional.

### 3.1.4 Logic Addition

Table 3.4: Logic Addition Options

| Option | Pro | Con
1 | A transistor is added to the IR emitter circuits. The PWM sig-nal from the processor will sup-ply the base with power. This causes the transistor and there-fore the IR emitting diodes to repeatedly switch on and off. While the IR emitting diodes are off, they do not draw power from the battery. | The Battery LiPo 800mAh has power limitations. The power dissipated by the IR emitting diodes over a period of time is halve the initial power dis-sipated. Therefore, double the current can be drawn and achieve the same initial power dissipated over a period of time. | The photo-transistor can only detect a wall when the IR emit-ting diodes are on i.e. there are periods of time when the photo-transisitor cannot detect a wall within range.
2 | No logic addition | The photo-transistor is contin-uously sensing whether there is a wall or not because the IR emitting diodes are always on. | The Battery LiPo 800mAh has power limitations. The current cannot be doubled without in-creasing the power drawn from the battery.

3.1. Design Decisions

Design decision: Option 1
In this design the IR emitting diodes can draw double the current without exceed the battery limitations. Double current through the diodes cause the diodes to emit a large amount of IR light. This increases the proximity at which the photo-transistor can detect walls. This is implemented for each IR emitter circuit. This is important to allow adequate time and space for the micro-mouse to avoid the wall. The photo-transistor will only be able to detect a wall when the IR emitting diode is on. However, this is not detrimental to the design. The micro-mouse will be relatively slow and the periods of no detection ability will be extremely small in comparison. Therefore, the micro-mouse will still have adequate time and space to avoid the wall despite the small delay in detection.

Note discarded design:
Option 2 could be chosen. The diodes would still emit enough IR light for the photo-transistor to detect walls. However, it will need to be closer to the wall to detect it, thus, leaving little room to avoid the wall. This will increase the time taken to avoid the wall and, ultimately, the time taken to navigate through a maze.

### 3.1.5 Component Selection

The design designs chosen in the IR Emitter and Circuitry subsection 3.1.1, the Power Supply subsection 3.1.2, the PCB Shape subsection 3.1.3 and Logic Addition subsection 3.1.4 require the following components: IR emitter, photo-transistor and transistor. E12 resistors and capacitors will be used, their values will be calculated in the calculations subsection 3.1.6.

Table 3.5: IR Emitting Diode Options

IR Emitting Diode | Radiant Power at Maximum Current | Rise/Fall Time | Total Cost | Stock
TSAL6200 | 40mW | 9ns | $4.3028 | 1047
SFH 7016 | 11mW | 15ns | $43.1 | 41

Table 3.6: Photo-transistor Options

Photo-transistor | Peak Sensitivity | Extra Feature | Total Cost | Stock
DY-PT204-6C | 940nm | | $3.1778 | 4963
QSD123 | 880nm | Daylight filter | $6.65 | 2
SFH 309 FA | 900nm | | $4.4876 | 1631

Table 3.7: Transistor Options

Transistor | Rise Time | Fall Time | Total Cost | Stock
MMBT3904 | 35nS | 50nS | $0.0582 | 1097041
PN2222ATA | 20nS | 60nS | $3.4634 | 9
2N2222A | 25nS | 60nS | $2.9972 | 23386

As per Table 3.5, IR Emitting Diode TSAL6200 is chosen due to it’s superior radiant power, short rise/fall time and low cost.
As per, Table 3.6, Photo-transistor SHF 309 FA is chosen due to its peak sensitivity aligning with IR Emitting Diode TSAL6200.

3.1. Design Decisions

As per Table 3.7, Transistor MMBT3904 is chosen due to its short rise/fall time and low total cost.

The stock of all components is greater than 1000 as per the specification to ensure the component will be available during maufacturing.

### 3.1.6 Calculations

The resistor values must be calculated to bias the components chosen in subsection 3.1.5 with the correct voltage and current for operation in the Emitter Circuit Figure 3.3 and Sensor Circuit Figure 3.4. The capacitor value must be chosen to effectively reduce noise in the Sensor Circuit Figure 3.4.

Emitter Circuit
Determine RB:
Set: PWM = 3.3V
Known: VBE = 0.95V
KVL: PWM − IBRB − VBE = 0
RB = 270Ω where IB = 8.7mA

Determine R1:
Known: BAT T = ±3.7V
Known: VCE = 1V
KVL: BAT T − IC1R1 − Vf − VCE = 0
R1 = 10Ω where IC1 = ±110mA

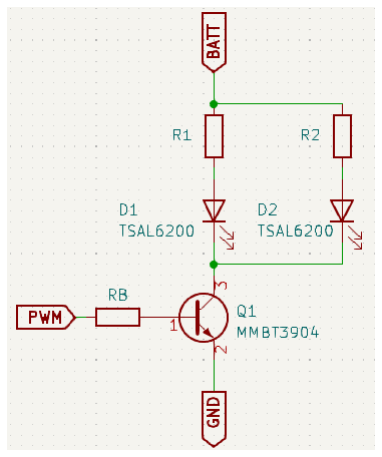
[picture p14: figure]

Similarly, R2 = 10Ω | Figure 3.3: Emitter Circuit

Sensor Circuit
Determine RS:
Known: 3V 3 Input
Known: IS and VCE varies depending on the amount of IR light the photo-transistor detects.
KVL: 3V 3 − VCE − ISRS = 0
RS = 10kΩ
A large value for RS was chosen to increase the output voltage, Analog, which is sent to the processor for interpretation.

Determine C:
Set: Output voltage, Analog, threshold is 2V .
The processor will indicate a wall when Analog > 2V .
A decoupling capacitor will reduce noise from the Analog output voltage. The capacitor value must fall within the range 10nF − 1uF.
C = 100nF

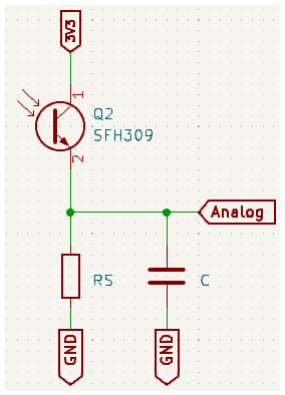
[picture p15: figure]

Figure 3.4: Sensor Circuit

3.1. Design Decisions

### 3.1.7 Final Design

The design consists of three Infrared Emitter circuits and three Infrared Proximity Sensor circuits for the left, centre and right sides of the PCB. The Infrared Emitter circuits emit IR light on the walls. The IR emitting diodes repeatedly switch on and off to save the battery’s power. The Infrared Proximity Sensor circuits detect the reflected IR light and outputs a corresponding analog voltage to the processor. If the output voltage is above the voltage threshold, 2V, the processor indicates a wall has been detected. A further analysis is seen in Figure 3.5 below. The design, component, resister and capacitor decisions were motivated in the previous subsections.

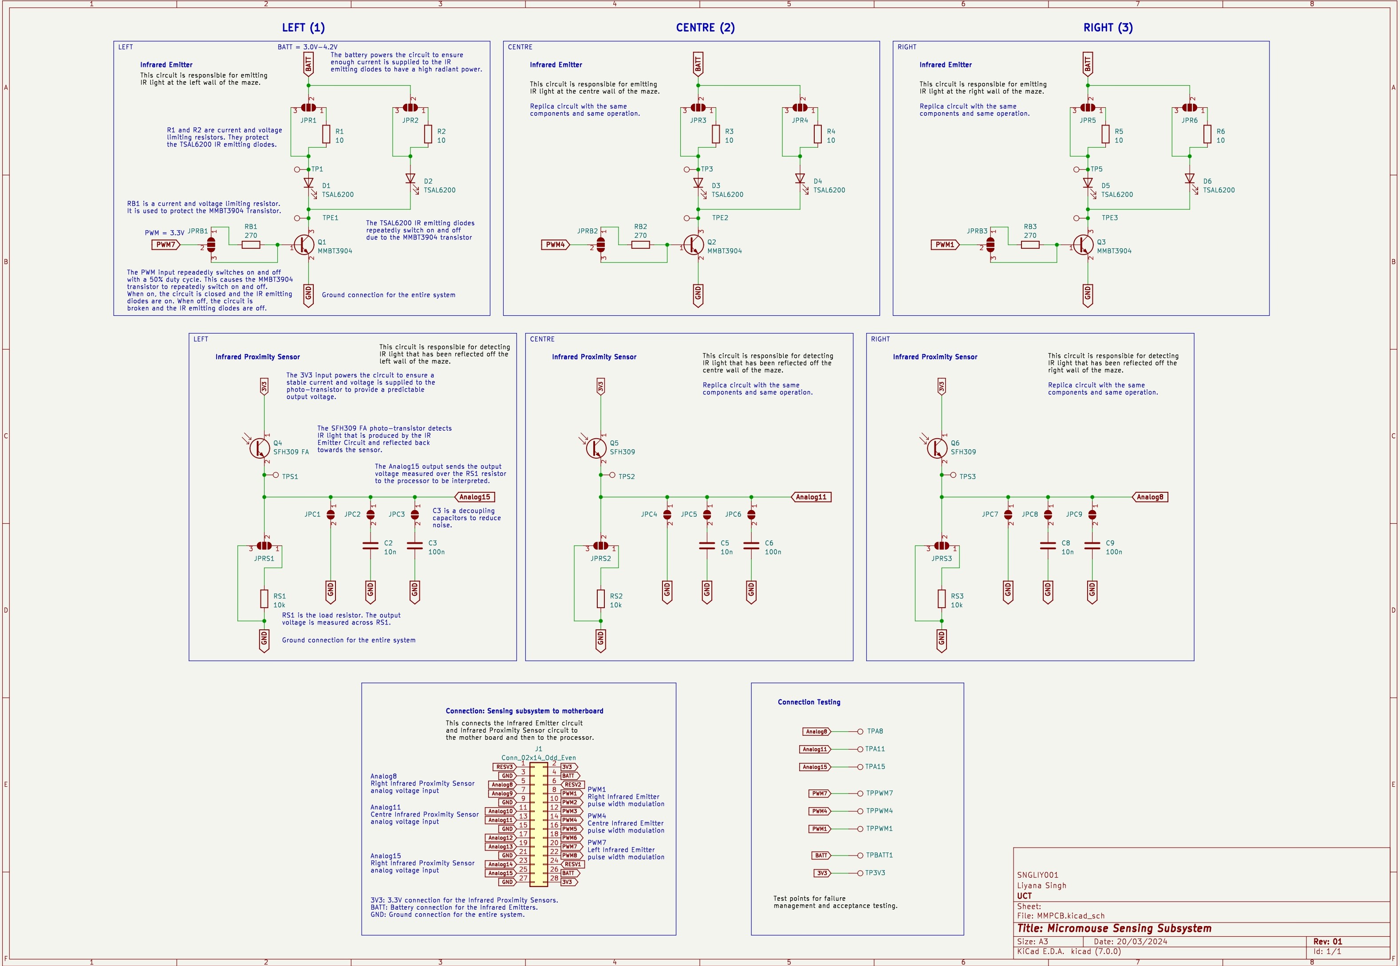
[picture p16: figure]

Figure 3.5: Schematic

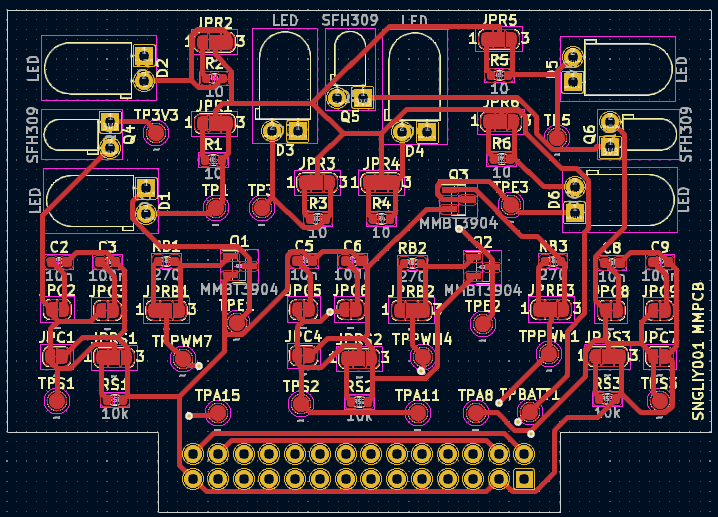
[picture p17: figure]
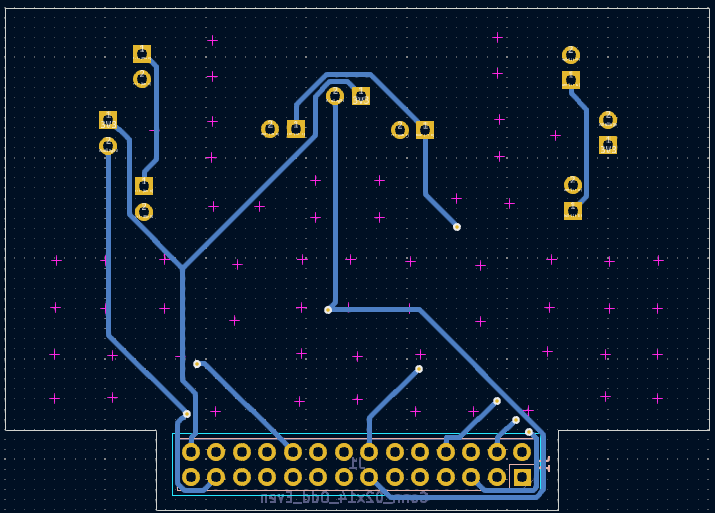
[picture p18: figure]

(a) Front PCB | (b) Back PCB | (c) 3D PCB

Figure 3.6: PCB

3.2. Failure Management

### 3.2 Failure Management

Please refer to the Schematic Figure 3.5 for the jumper and test point positions.

Table 3.8: Failure Management

Name | Description
Resistor Jumpers | Every resistor in the schematic has a three pad jumper. The jumper can be used to connect the current resistor to the circuit as calculated. However, if there is a calculation error, a second resistor can be added to the circuit in place of the incorrect resistor.
Capacitor Jumpers and Additional Ca-pacitors | The capacitor has a two pad jumper. The capacitor C3 = C6 = C9 = 100nF as calculated can be connected. However, the additional capacitor C2 = C5 = C8 = 10nF can be connected instead. If neither are correct, a third capacitor C1 = C4 = C7 can be chosen and connected to replace the other two.
Tractability Infrared Emitter Circuit | Test points TP1, TP2 and TP3 in conjunction with TPE1, TPE2 and TPE3 are used to measure voltage at significant points in the circuit. The voltage over the IR emitting diodes and the collector emitter voltage of the transistors can be tested.
Tractability Infrared Proximity Circuit | The test points TPS1, TPS2 and TPS3 in conjunction with TPA15, TPA11 and TPA8 are used to measure voltage at significant points in the circuit. The voltage over the load resistor and the output voltage sent to the processor.

### 3.3 System Integration and Interfacing

Table 3.9: Interfacing Specifications

ID | Interface | Description | Pins/Output
I1 | J1 | Power supplied from processor subsystem (STM32L476) to sensing subsystem | • 3V0-4V2: STM BATT to PIN04 • 3V3: STM 3V3 to PIN02
I2 | J1 | PWM signals from processor subsystem (STM32L476) to sensing subsystem | • PWM1: STM PE15 to PIN08 • PWM4: STM PE12 to PIN14 • PWM7: STM PE9 to PIN20
I3 | J1 | Analog output voltage from sensing subsystem to processor subsystem (STM32L476) | • Analog8: PIN05 to STM PA3 • Analog11: PIN13 to STM PA6 • Analog15: PIN25 to STM AB0
I4 | J1 | Sensing subsystem ground to processor subsystem (STM32L476) ground | • GND: PIN21 to STM GND

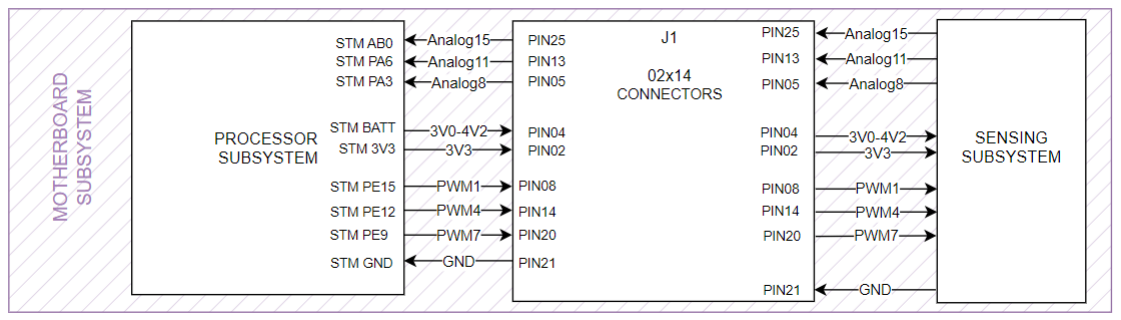
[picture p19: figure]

Figure 3.7: Interfacing Diagram

# Chapter 4

# Acceptance Testing

### 4.1 Tests

Table 4.1: Acceptance Tests

Test ID | Description | Testing Procedure | Pass/Fail Criteria
AT01 | Measure voltage across IR emitter circuitry. | • Use a multi-meter to measure across the test point TPBATT1 and GND. | • Voltage is 3V3-4V2.
AT02 | Measure voltage across IR sensor circuitry. | • Use a multi-meter to measure across the test point TP3V3 and GND. | • Voltage is 3V3. • Voltage is stable.
AT03 | Measure the current through the IR emitter circuit. | • Assume AT01 passed. • Use an oscilloscope to measure across pad1 and pad2 of jumper JPR1, JPR2 and JPR3. • Add the average currents together. | • Current is below 360mA.
AT04 | Measure the current through the IR sensor circuit. | • Assume AT02 passed. • Use an oscilloscope to measure across pad1 and pad2 of jumper JPRS1, JPRS2 and JPRS3. • Add the currents together. | • Current is below 40mA.
AT05 | Check there is IR emit-ter circuitry and IR sensor circuitry for the front, left and right sides of the PCB. | • Observe the PCB. | • Two front facing, right facing and left facing TSAL6200 IR emitting diodes. • One front facing, right facing and left facing SFH 309 FA photo-transistor.
AT06 | The processor board has three LEDs. Observe LED1, LED2 and LED3 which indicate a wall is sensed on the left, front and right, respectively, by turning on. If no wall is sensed, then no LEDs will be on. | • Assume AT01, AT02, AT03, AT04 and AT05 have passed. • Observe the three LEDs. • Bring a section of the maze wall to the left of the PCB • Bring a section of the maze wall to the front of the PCB • Bring a section of the maze wall to the right of the PCB | • Initially no LEDs are on. • Then LED1 turns on. • Then LED2 turns on. • Then LED3 turns on.

4.1. Tests
Test ID | Description | Testing Procedure | Pass/Fail Criteria
AT07 | Measure the output volt-age of the IR sensor cir-cuitry. | • Assume AT01, AT02, AT03, AT04 and AT05 have passed. • Use a multi-meter to mea-sure the output voltage on TPA8, TPA11 and TPA15. • Bring a section of the maze wall to the left of the PCB. Measure the voltage at TPA8. • Bring a section of the maze wall to the front of the PCB. Measure the voltage at TPA11. • Bring a section of the maze wall to the right of the PCB. Measure the voltage at TPA15. | • Initially the voltage at TPA8, TPA11 and TPA15 are 0V. • Then TPA8 is >2V. • Then TPA11 is >2V. • Then TPA15 is >2V.
AT08 | Measure the pin pitch on the sensing PCB. | • Use a caliper to measure the diameter of the pin pitch holes. | • The pin pitch is <=2.54mm
AT09 | Measure the PCB’s length and width. | • Use a PCB ruler to measure the length of the PCB. • Use a PCB ruler to measure the width of the PCB. | • The length of the PCB <=80mm. • The width of the PCB <=80mm.
AT10 | Check PCB cost is within budget. | • Review the JLCPCB web-site order. | • The total order for two PCBs is <=30$
AT11 | Check component avail-ability. | • Check the JLCPCB manu-facturing bill of materials. | • All components appear on the manufacturing bill of materials.

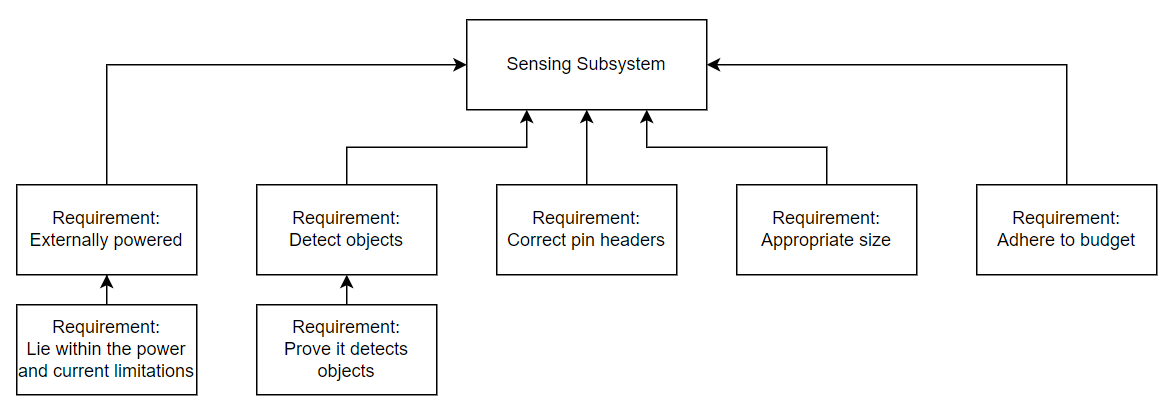
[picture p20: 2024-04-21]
documents/sensing/diagrams/Highlevel_Requirements_Diagram_MM.png

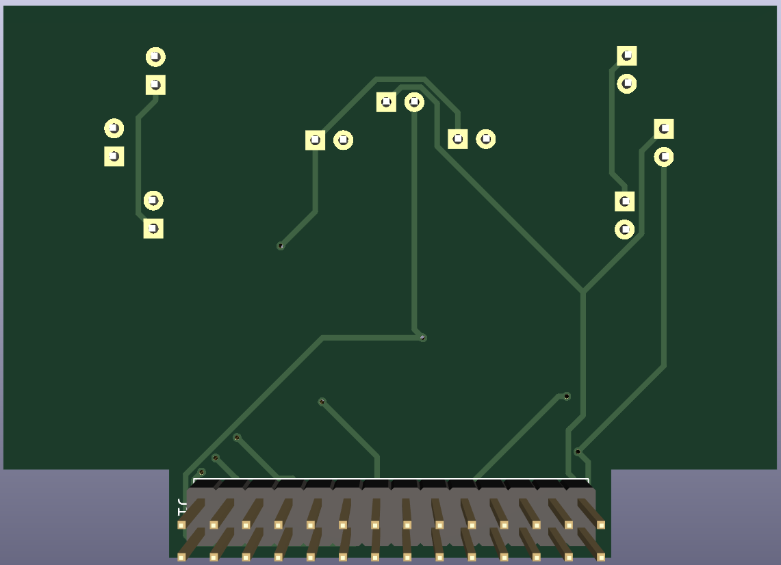
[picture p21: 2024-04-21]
documents/sensing/diagrams/PCBBack.png

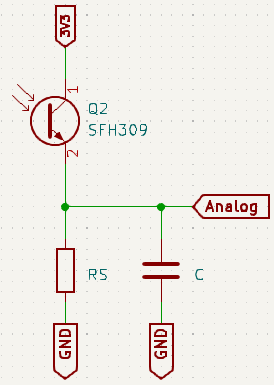
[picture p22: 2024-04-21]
documents/sensing/diagrams/Sensorcalc.png

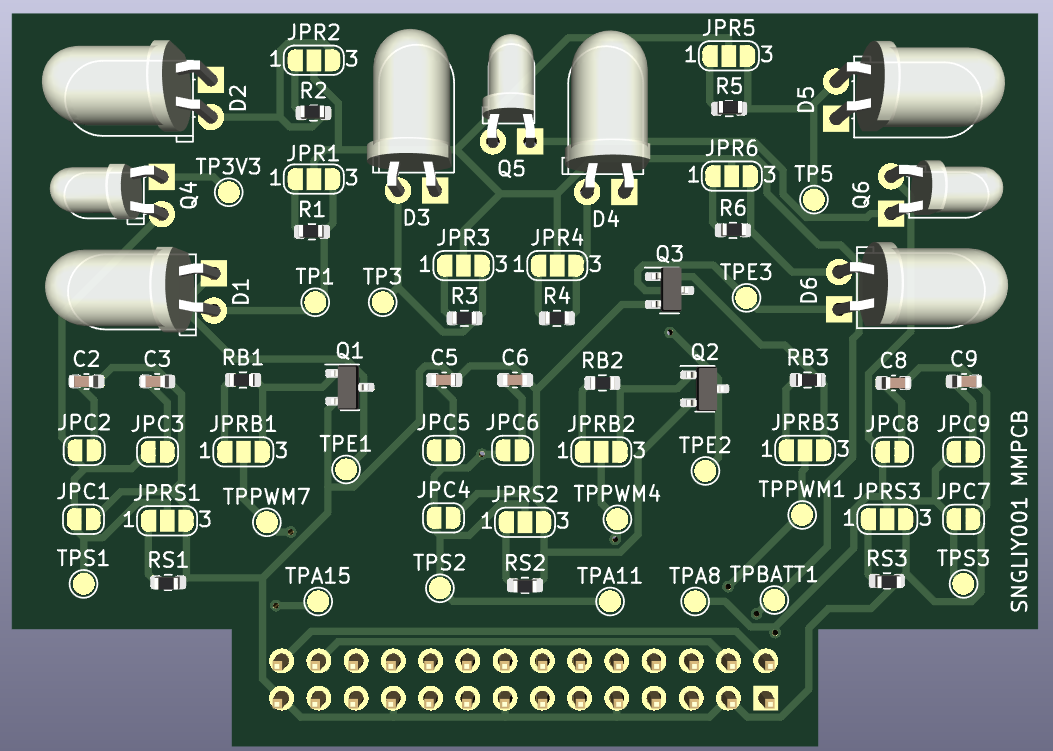
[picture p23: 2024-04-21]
documents/sensing/diagrams/PCBFront.png

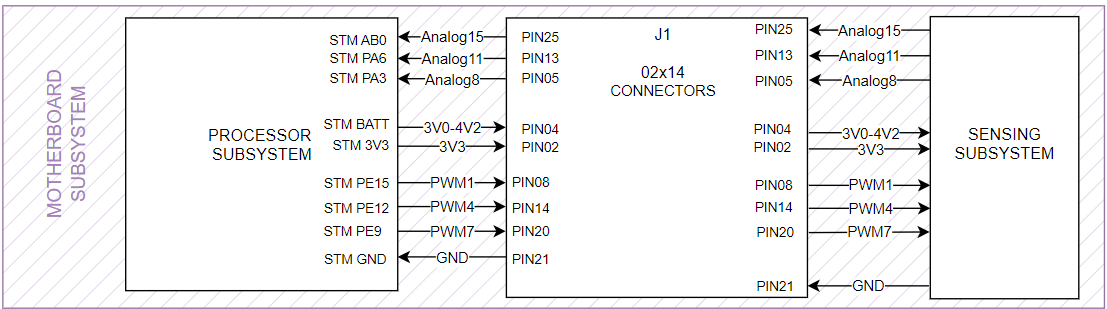
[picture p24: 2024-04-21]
documents/sensing/diagrams/InterfacingDiagram1.png

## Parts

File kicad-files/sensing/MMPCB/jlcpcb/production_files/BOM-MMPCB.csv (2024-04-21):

Comment | Designator | Footprint | LCSC
100n | C3,C6,C9 | C_0603_1608Metric | C14663
MMBT3904 | Q1,Q2,Q3 | SOT-23 | C20526
10 | R1,R2,R3,R4,R5,R6 | R_0603_1608Metric | C22859
270 | RB1,RB2,RB3 | R_0603_1608Metric | C22966
10k | RS1,RS2,RS3 | R_0603_1608Metric | C25804
SFH309 | Q4,Q5,Q6 | LED_D3.0mm_Horizontal_O1.27mm_Z2.0mm_Clear | C2900253
LED | D1,D2,D3,D4,D5,D6 | LED_D5.0mm_Horizontal_O1.27mm_Z3.0mm_Clear | C55528
10n | C2,C5,C8 | C_0603_1608Metric | C57112

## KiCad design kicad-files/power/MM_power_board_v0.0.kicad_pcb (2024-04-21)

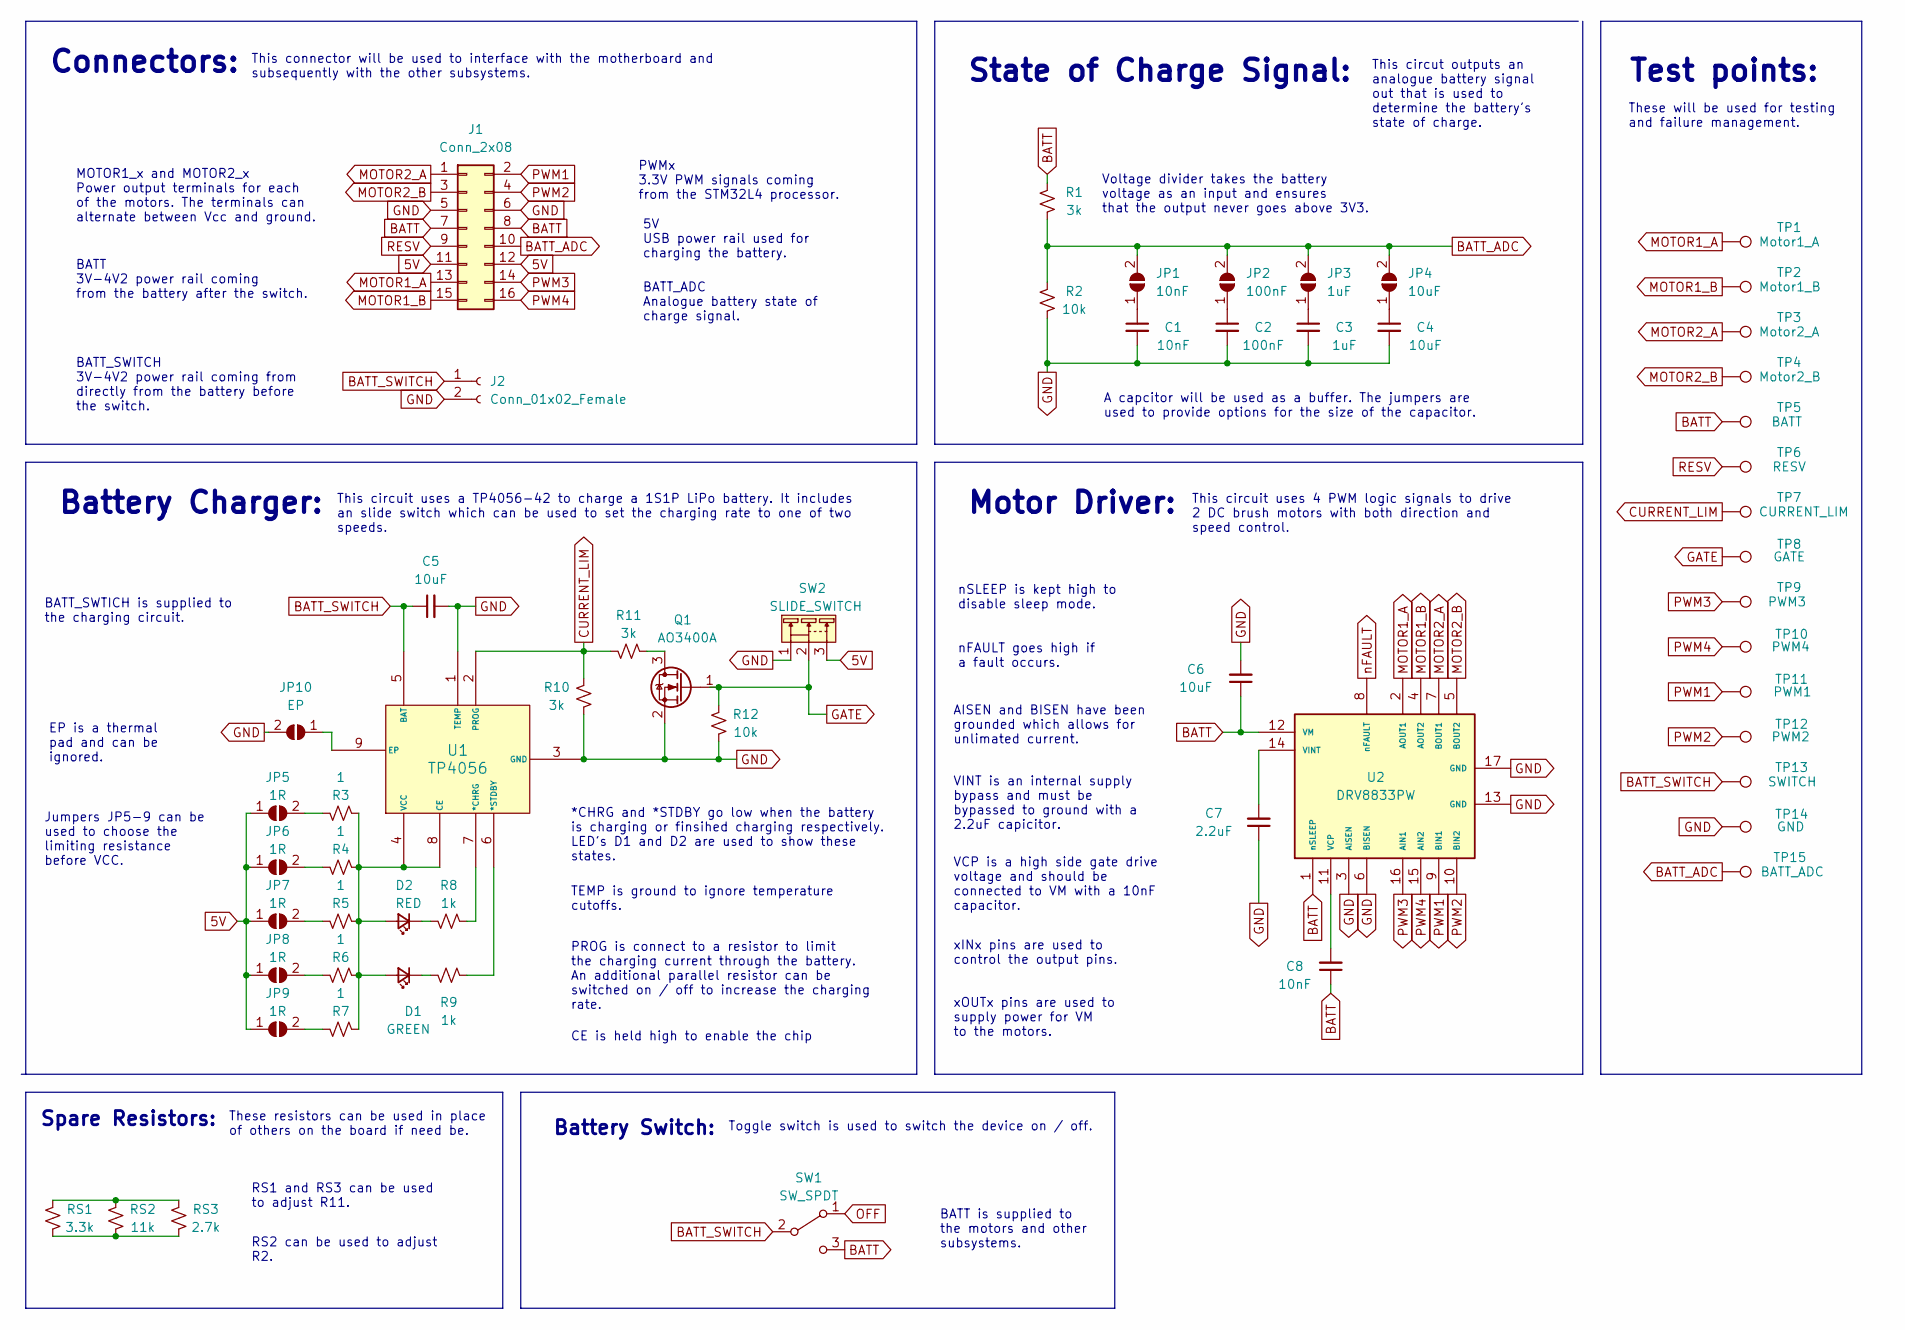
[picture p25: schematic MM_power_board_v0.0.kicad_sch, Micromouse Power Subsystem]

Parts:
C1, C8: 10nF; C_0603_1608Metric
C2: 100nF; C_0603_1608Metric
C3: 1uF; C_0603_1608Metric
C4, C5, C6: 10uF; C_0603_1608Metric
C7: 2.2uF; C_0603_1608Metric
D1: GREEN; LED0805-R-RD
D2: RED; LED0603-RD
J1: Conn_2x08; PinHeader_2x08_P2.54mm_Vertical
J2: Conn_01x02_Female; JST_PH_S2B-PH-K_1x02_P2.00mm_Horizontal
JP1: 10nF; SolderJumper-2_P1.3mm_Open_RoundedPad1.0x1.5mm
JP2: 100nF; SolderJumper-2_P1.3mm_Open_RoundedPad1.0x1.5mm
JP3: 1uF; SolderJumper-2_P1.3mm_Open_RoundedPad1.0x1.5mm
JP4: 10uF; SolderJumper-2_P1.3mm_Open_RoundedPad1.0x1.5mm
JP5, JP6, JP7, JP8, JP9: 1R; SolderJumper-2_P1.3mm_Open_RoundedPad1.0x1.5mm
JP10: EP; SolderJumper-2_P1.3mm_Open_RoundedPad1.0x1.5mm
Q1: AO3400A; SOT-23
R1, R10, R11: 3k; R_0603_1608Metric
R2, R12: 10k; R_0603_1608Metric
R3, R4, R5, R6, R7: 1; R_1206_3216Metric
R8, R9: 1k; R_0603_1608Metric
RS1: 3.3k; R_0603_1608Metric
RS2: 11k; R_0603_1608Metric
RS3: 2.7k; R_0603_1608Metric
SW1: SW_SPDT; SW-TH_MT-0-103-A101-M200-RS
SW2: SLIDE_SWITCH; SW-TH_SS-12D10L5
TP1: Motor1_A; TestPoint_Keystone_5000-5004_Miniature
TP2: Motor1_B; TestPoint_Keystone_5000-5004_Miniature
TP3: Motor2_A; TestPoint_Keystone_5000-5004_Miniature
TP4: Motor2_B; TestPoint_Keystone_5000-5004_Miniature
TP5: BATT; TestPoint_Keystone_5000-5004_Miniature
TP6: RESV; TestPoint_Keystone_5000-5004_Miniature
TP7: CURRENT_LIM; TestPoint_Keystone_5000-5004_Miniature
TP8: GATE; TestPoint_Keystone_5000-5004_Miniature
TP9: PWM3; TestPoint_Keystone_5000-5004_Miniature
TP10: PWM4; TestPoint_Keystone_5000-5004_Miniature
TP11: PWM1; TestPoint_Keystone_5000-5004_Miniature
TP12: PWM2; TestPoint_Keystone_5000-5004_Miniature
TP13: SWITCH; TestPoint_Keystone_5000-5004_Miniature
TP14: GND; TestPoint_Keystone_5000-5004_Miniature
TP15: BATT_ADC; TestPoint_Keystone_5000-5004_Miniature
U1: TP4056; ESOP-8_L4.9-W3.9-P1.27-LS6.0-BL-EP
U2: DRV8833PW; TSSOP-16_L5.0-W4.4-P0.65-LS6.4-BL-EP

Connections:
5V: J1.11, J1.12, JP5.1 (A), JP6.1 (A), JP7.1 (A), JP8.1 (A), JP9.1 (A), SW2.3
BATT: C6.1, C8.1, J1.7, J1.8, R1.2, SW1.3 (C), TP5.1, U2.1 (nSLEEP), U2.12 (VM)
BATT_ADC: J1.10, JP1.2 (B), JP2.2 (B), JP3.2 (B), JP4.2 (B), R1.1, R2.2, TP15.1
BATT_SWITCH: C5.1, J2.1, SW1.2 (B), TP13.1, U1.5 (BAT)
CURRENT_LIM: R10.2, R11.1, TP7.1, U1.2 (PROG)
GATE: Q1.1 (G), R12.1, SW2.2, TP8.1
GND: C1.2, C2.2, C3.2, C4.2, C5.2, C6.2, C7.1, J1.5, J1.6, J2.2, JP10.2 (B), Q1.2 (S), R2.1, R10.1, R12.2, SW2.1, TP14.1, U1.1 (TEMP), U1.3 (GND), U2.3 (AISEN), U2.6 (BISEN), U2.13 (GND), U2.17 (GND)
Motor1_A: J1.13, TP1.1, U2.2 (AOUT1)
Motor1_B: J1.15, TP2.1, U2.4 (AOUT2)
Motor2_A: J1.1, TP3.1, U2.7 (BOUT1)
Motor2_B: J1.3, TP4.1, U2.5 (BOUT2)
unnamed: C1.1, JP1.1 (A)
unnamed: C2.1, JP2.1 (A)
unnamed: C3.1, JP3.1 (A)
unnamed: C4.1, JP4.1 (A)
unnamed: C7.2, U2.14 (VINT)
unnamed: C8.2, U2.11 (VCP)
unnamed: D1.1 (K), R9.2
unnamed: D1.2 (A), D2.2 (A), R3.2, R4.2, R5.2, R6.2, R7.2, U1.4 (VCC), U1.8 (CE)
unnamed: D2.1 (K), R8.2
unnamed: JP5.2 (B), R3.1
unnamed: JP6.2 (B), R4.1
unnamed: JP7.2 (B), R5.1
unnamed: JP8.2 (B), R6.1
unnamed: JP9.2 (B), R7.1
unnamed: JP10.1 (A), U1.9 (EP)
unnamed: Q1.3 (D), R11.2
unnamed: R8.1, U1.7 (*CHRG)
unnamed: R9.1, U1.6 (*STDBY)
unnamed: RS1.1, RS2.1, RS3.1
unnamed: RS1.2, RS2.2, RS3.2
OFF: SW1.1 (A)
PWM1: J1.2, TP11.1, U2.9 (BIN1)
PWM2: J1.4, TP12.1, U2.10 (BIN2)
PWM3: J1.14, TP9.1, U2.16 (AIN1)
PWM4: J1.16, TP10.1, U2.15 (AIN2)
RESV: J1.9, TP6.1
nFAULT: U2.8 (nFAULT)

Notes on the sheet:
BATT is supplied to the motors and other subsystems.
EP is a thermal pad and can be ignored.
Battery Charger:
Jumpers JP5-9 can be used to choose the limiting resistance before VCC.
Voltage divider takes the battery voltage as an input and ensures that the output never goes above 3V3.
A capcitor will be used as a buffer. The jumpers are used to provide options for the size of the capacitor.
VINT is an internal supply bypass and must be bypassed to ground with a 2.2uF capicitor.
This circuit uses 4 PWM logic signals to drive 2 DC brush motors with both direction and speed control.
These resistors can be used in place of others on the board if need be.
BATT_ADC Analogue battery state of charge signal.
nFAULT goes high if a fault occurs.
State of Charge Signal:
These will be used for testing and failure management.
BATT 3V-4V2 power rail coming from the battery after the switch.
This circut outputs an analogue battery signal out that is used to determine the battery's state of charge.
RS2 can be used to adjust R2.
PROG is connect to a resistor to limit the charging current through the battery. An additional parallel resistor can be switched on / off to increase the charging rate.
BATT_SWITCH 3V-4V2 power rail coming from directly from the battery before the switch.
CE is held high to enable the chip
VCP is a high side gate drive voltage and should be connected to VM with a 10nF capacitor.
Connectors:
Battery Switch:
This connector will be used to interface with the motherboard and subsequently with the other subsystems.
xINx pins are used to control the output pins.
PWMx 3.3V PWM signals coming from the STM32L4 processor.
xOUTx pins are used to supply power for VM to the motors.
Spare Resistors:
TEMP is ground to ignore temperature cutoffs.
AISEN and BISEN have been grounded which allows for unlimated current.
RS1 and RS3 can be used to adjust R11.
5V USB power rail used for charging the battery.
Test points:
nSLEEP is kept high to disable sleep mode.
BATT_SWTICH is supplied to the charging circuit.
MOTOR1_x and MOTOR2_x Power output terminals for each of the motors. The terminals can alternate between Vcc and ground.
Toggle switch is used to switch the device on / off.
Motor Driver:
*CHRG and *STDBY go low when the battery is charging or finsihed charging respectively. LED's D1 and D2 are used to show these states.
This circuit uses a TP4056-42 to charge a 1S1P LiPo battery. It includes an slide switch which can be used to set the charging rate to one of two speeds.

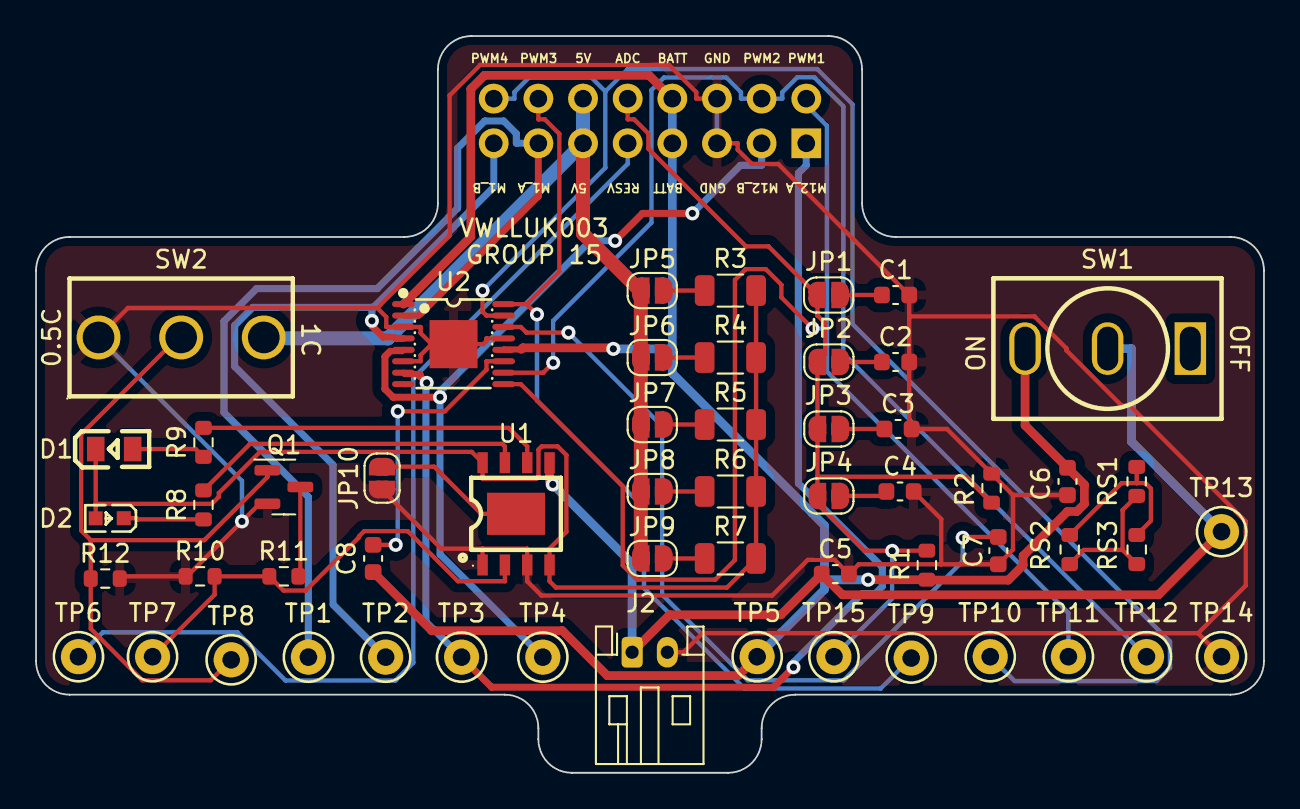
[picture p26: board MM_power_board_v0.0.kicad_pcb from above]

Board: 2 copper layers, 69.9 x 41.9 mm, 57 parts (1 on the bottom side), 36 nets.

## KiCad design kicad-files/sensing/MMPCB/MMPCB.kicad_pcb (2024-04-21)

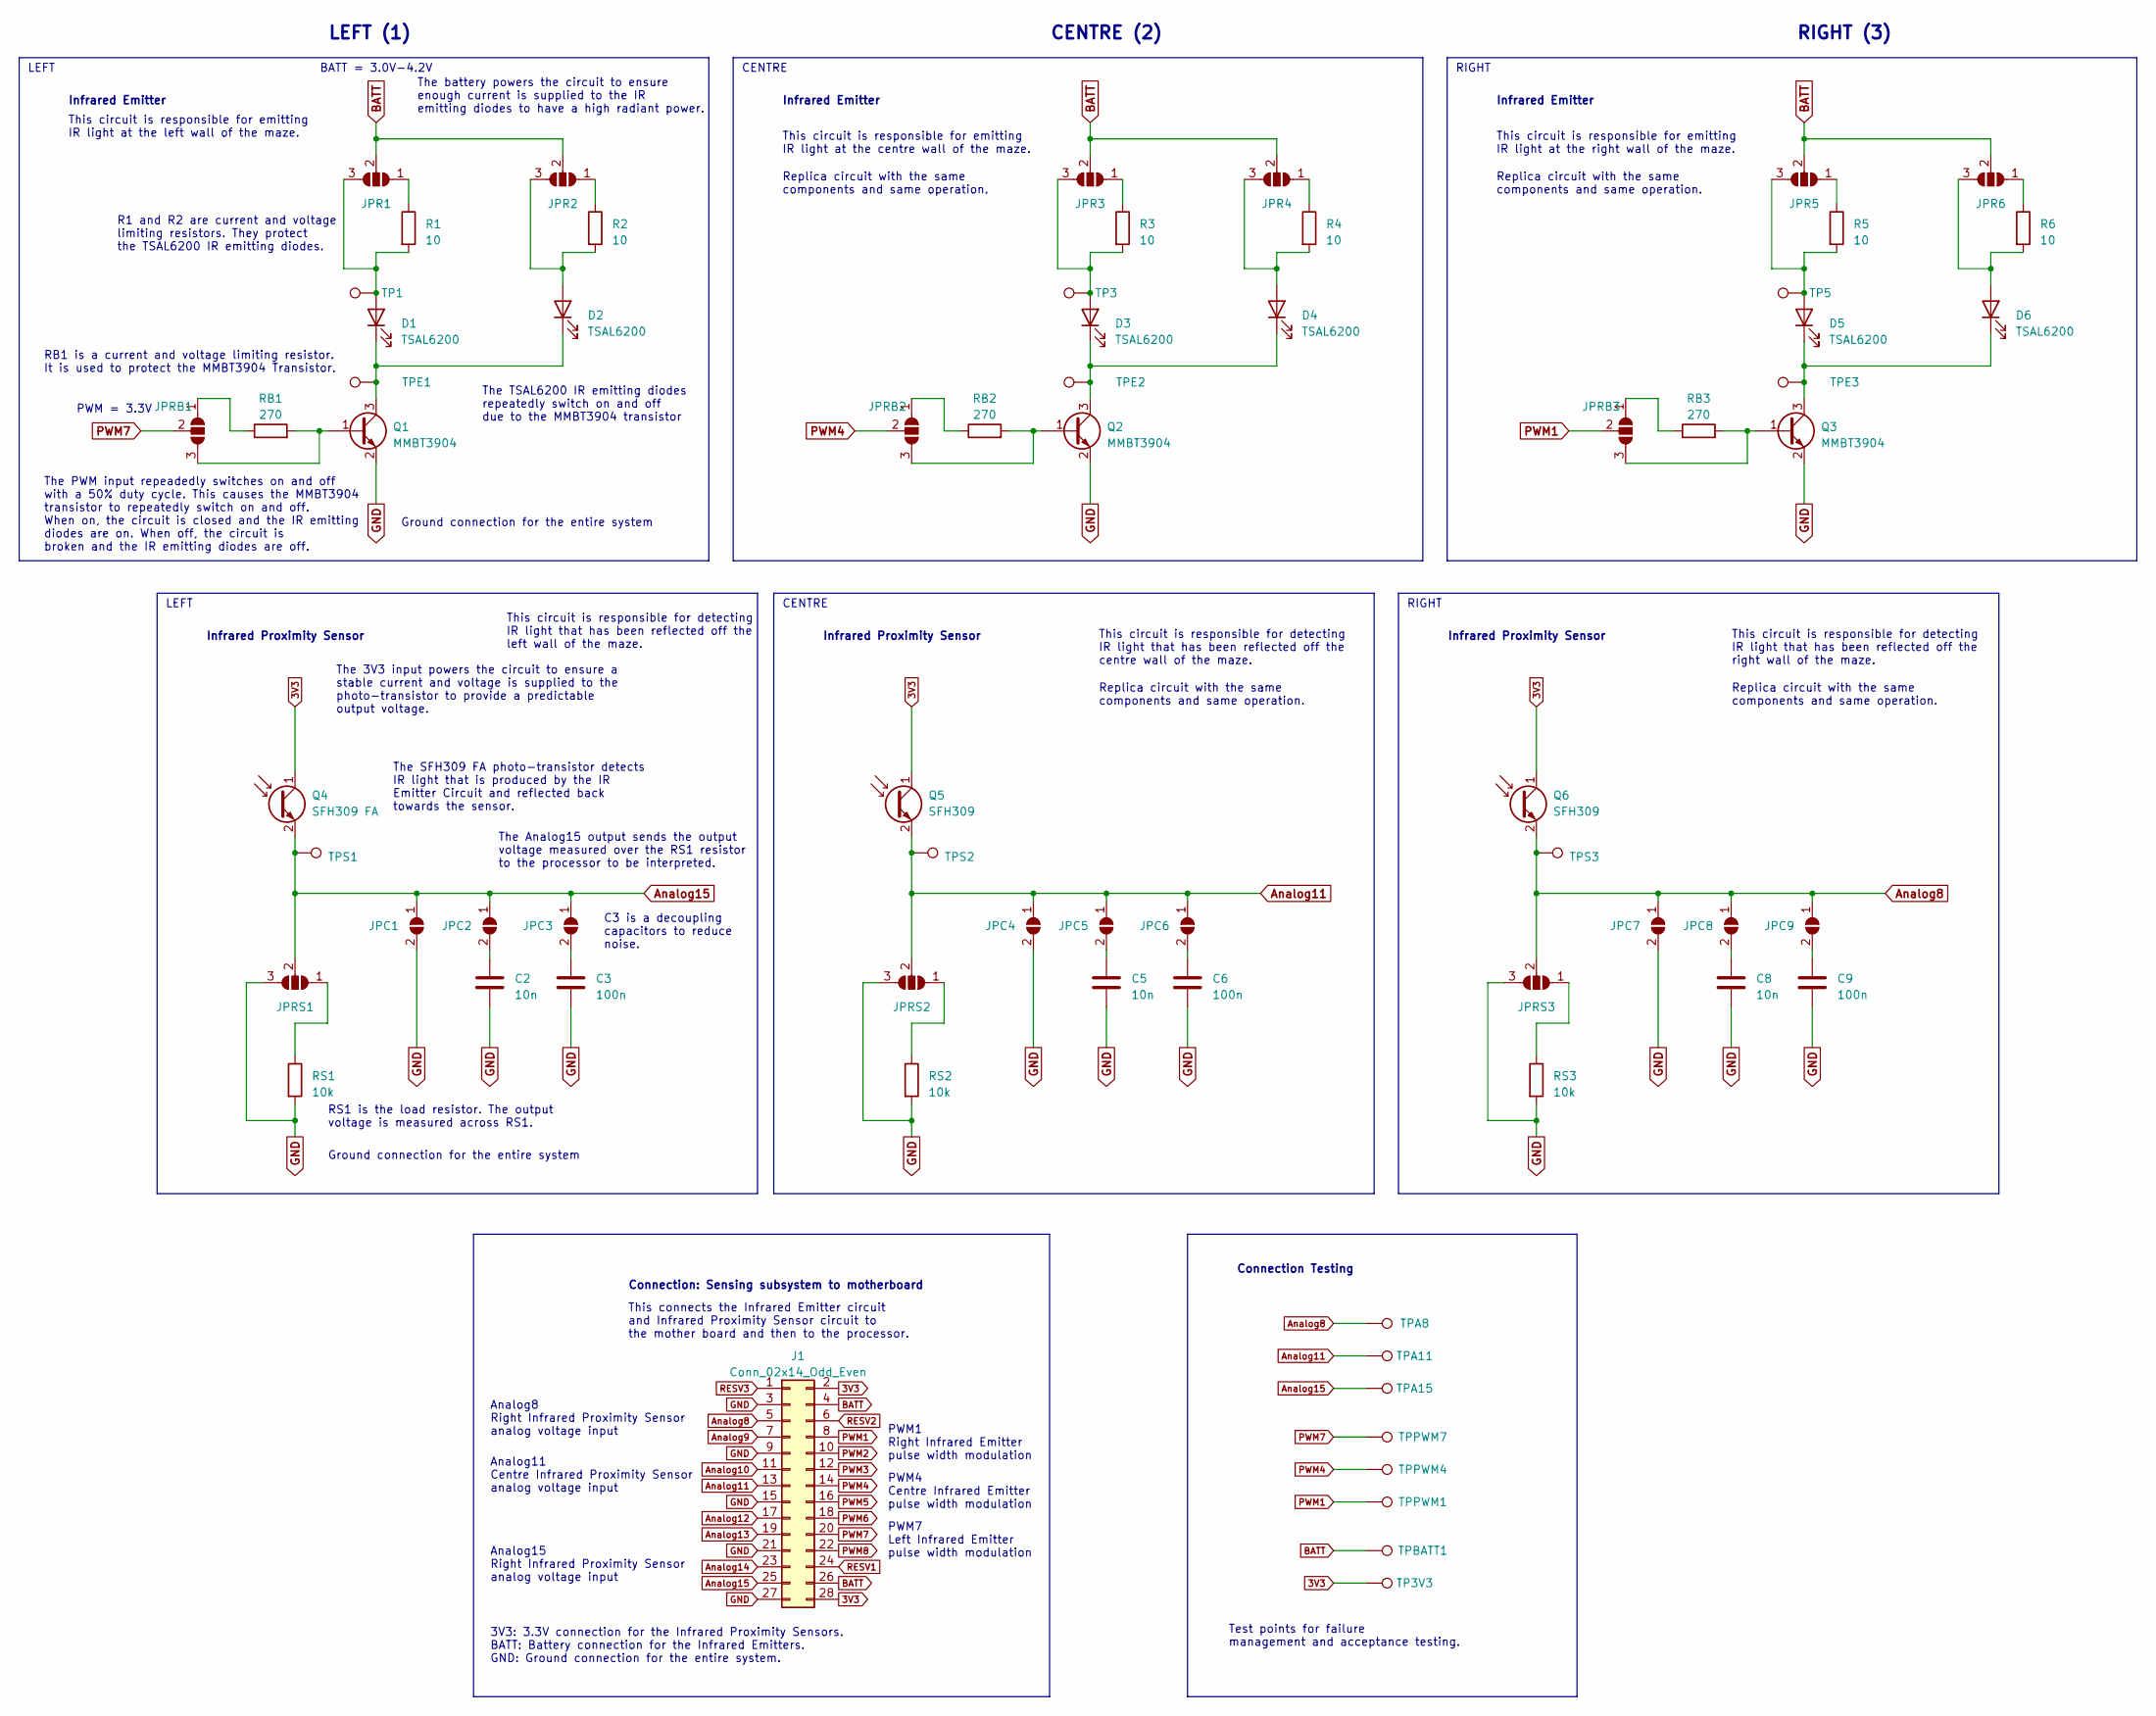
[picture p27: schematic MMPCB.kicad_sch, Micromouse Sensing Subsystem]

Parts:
C2, C5, C8: 10n; C_0603_1608Metric
C3, C6, C9: 100n; C_0603_1608Metric
D1, D2, D3, D4, D5, D6: TSAL6200; LED_D5.0mm_Horizontal_O1.27mm_Z3.0mm_Clear
J1: Conn_02x14_Odd_Even; PinHeader_2x14_P2.54mm_Vertical
JPC1, JPC2, JPC3, JPC4, JPC5, JPC6, JPC7, JPC8, JPC9: SolderJumper-2_P1.3mm_Open_RoundedPad1.0x1.5mm
JPR1, JPR2, JPR3, JPR4, JPR5, JPR6: SolderJumper-3_P1.3mm_Open_RoundedPad1.0x1.5mm_NumberLabels
JPRB1, JPRB2, JPRB3: SolderJumper-3_P1.3mm_Open_RoundedPad1.0x1.5mm_NumberLabels
JPRS1, JPRS2, JPRS3: SolderJumper-3_P1.3mm_Open_RoundedPad1.0x1.5mm_NumberLabels
Q1, Q2, Q3: MMBT3904; SOT-23
Q4: SFH309 FA; LED_D3.0mm_Horizontal_O1.27mm_Z2.0mm_Clear
Q5, Q6: SFH309; LED_D3.0mm_Horizontal_O1.27mm_Z2.0mm_Clear
R1, R2, R3, R4, R5, R6: 10; R_0603_1608Metric
RB1, RB2, RB3: 270; R_0603_1608Metric
RS1, RS2, RS3: 10k; R_0603_1608Metric
TP1, TP3, TP3V3, TP5: TestPoint_Pad_D1.5mm
TPA8, TPA11, TPA15: TestPoint_Pad_D1.5mm
TPBATT1: TestPoint_Pad_D1.5mm
TPE1, TPE2, TPE3: TestPoint_Pad_D1.5mm
TPPWM1, TPPWM4, TPPWM7: TestPoint_Pad_D1.5mm
TPS1, TPS2, TPS3: TestPoint_Pad_D1.5mm

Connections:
3V3: J1.2, J1.28, Q4.1 (C), Q5.1 (C), Q6.1 (C), TP3V3.1
Analog8: J1.5, JPC7.1 (A), JPC8.1 (A), JPC9.1 (A), JPRS3.2 (C), Q6.2 (E), TPA8.1, TPS3.1
Analog9: J1.7
Analog10: J1.11
Analog11: J1.13, JPC4.1 (A), JPC5.1 (A), JPC6.1 (A), JPRS2.2 (C), Q5.2 (E), TPA11.1, TPS2.1
Analog12: J1.17
Analog13: J1.19
Analog14: J1.23
Analog15: J1.25, JPC1.1 (A), JPC2.1 (A), JPC3.1 (A), JPRS1.2 (C), Q4.2 (E), TPA15.1, TPS1.1
BATT: J1.4, J1.26, JPR1.2 (C), JPR2.2 (C), JPR3.2 (C), JPR4.2 (C), JPR5.2 (C), JPR6.2 (C), TPBATT1.1
GND: C2.2, C3.2, C5.2, C6.2, C8.2, C9.2, J1.3, J1.9, J1.15, J1.21, J1.27, JPC1.2 (B), JPC4.2 (B), JPC7.2 (B), JPRS1.3 (B), JPRS2.3 (B), JPRS3.3 (B), Q1.2 (E), Q2.2 (E), Q3.2 (E), RS1.2, RS2.2, RS3.2
unnamed: D1.2 (A), JPR1.3 (B), R1.2, TP1.1
unnamed: D1.1 (K), D2.1 (K), Q1.3 (C), TPE1.1
unnamed: D2.2 (A), JPR2.3 (B), R2.2
unnamed: D3.2 (A), JPR3.3 (B), R3.2, TP3.1
unnamed: D3.1 (K), D4.1 (K), Q2.3 (C), TPE2.1
unnamed: D4.2 (A), JPR4.3 (B), R4.2
unnamed: D5.2 (A), JPR5.3 (B), R5.2, TP5.1
unnamed: D5.1 (K), D6.1 (K), Q3.3 (C), TPE3.1
unnamed: D6.2 (A), JPR6.3 (B), R6.2
unnamed: C2.1, JPC2.2 (B)
unnamed: C3.1, JPC3.2 (B)
unnamed: C5.1, JPC5.2 (B)
unnamed: C6.1, JPC6.2 (B)
unnamed: C8.1, JPC8.2 (B)
unnamed: C9.1, JPC9.2 (B)
unnamed: JPR1.1 (A), R1.1
unnamed: JPR2.1 (A), R2.1
unnamed: JPR3.1 (A), R3.1
unnamed: JPR4.1 (A), R4.1
unnamed: JPR5.1 (A), R5.1
unnamed: JPR6.1 (A), R6.1
unnamed: JPRB1.1 (A), RB1.1
unnamed: JPRB1.3 (B), Q1.1 (B), RB1.2
unnamed: JPRB2.1 (A), RB2.1
unnamed: JPRB2.3 (B), Q2.1 (B), RB2.2
unnamed: JPRB3.1 (A), RB3.1
unnamed: JPRB3.3 (B), Q3.1 (B), RB3.2
unnamed: JPRS1.1 (A), RS1.1
unnamed: JPRS2.1 (A), RS2.1
unnamed: JPRS3.1 (A), RS3.1
PWM1: J1.8, JPRB3.2 (C), TPPWM1.1
PWM2: J1.10
PWM3: J1.12
PWM4: J1.14, JPRB2.2 (C), TPPWM4.1
PWM5: J1.16
PWM6: J1.18
PWM7: J1.20, JPRB1.2 (C), TPPWM7.1
PWM8: J1.22
RESV1: J1.24
RESV2: J1.6
RESV3: J1.1

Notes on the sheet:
Test points for failure management and acceptance testing.
This connects the Infrared Emitter circuit and Infrared Proximity Sensor circuit to the mother board and then to the processor.
RIGHT
The SFH309 FA photo-transistor detects IR light that is produced by the IR Emitter Circuit and reflected back towards the sensor.
Analog11 Centre Infrared Proximity Sensor analog voltage input
Replica circuit with the same components and same operation.
LEFT
Infrared Proximity Sensor
PWM7 Left Infrared Emitter pulse width modulation
The PWM input repeadedly switches on and off with a 50% duty cycle. This causes the MMBT3904 transistor to repeatedly switch on and off. When on, the circuit is closed and the IR emitting diodes are on. When off, the circuit is broken and the IR emitting diodes are off.
This circuit is responsible for detecting IR light that has been reflected off the left wall of the maze.
C3 is a decoupling capacitors to reduce noise.
Analog8 Right Infrared Proximity Sensor analog voltage input
This circuit is responsible for emitting IR light at the left wall of the maze.
This circuit is responsible for detecting IR light that has been reflected off the centre wall of the maze.
The 3V3 input powers the circuit to ensure a stable current and voltage is supplied to the photo-transistor to provide a predictable output voltage.
PWM1 Right Infrared Emitter pulse width modulation
PWM = 3.3V
Connection Testing
This circuit is responsible for emitting IR light at the centre wall of the maze.
The Analog15 output sends the output voltage measured over the RS1 resistor to the processor to be interpreted.
RS1 is the load resistor. The output voltage is measured across RS1.
LEFT (1)
Infrared Emitter
RIGHT (3)
This circuit is responsible for detecting IR light that has been reflected off the right wall of the maze.
BATT = 3.0V-4.2V
Ground connection for the entire system
PWM4 Centre Infrared Emitter pulse width modulation
Analog15 Right Infrared Proximity Sensor analog voltage input
CENTRE (2)
The TSAL6200 IR emitting diodes repeatedly switch on and off due to the MMBT3904 transistor
CENTRE
3V3: 3.3V connection for the Infrared Proximity Sensors. BATT: Battery connection for the Infrared Emitters. GND: Ground connection for the entire system.
R1 and R2 are current and voltage limiting resistors. They protect the TSAL6200 IR emitting diodes.
This circuit is responsible for emitting IR light at the right wall of the maze.
Connection: Sensing subsystem to motherboard
The battery powers the circuit to ensure enough current is supplied to the IR emitting diodes to have a high radiant power.
RB1 is a current and voltage limiting resistor. It is used to protect the MMBT3904 Transistor.

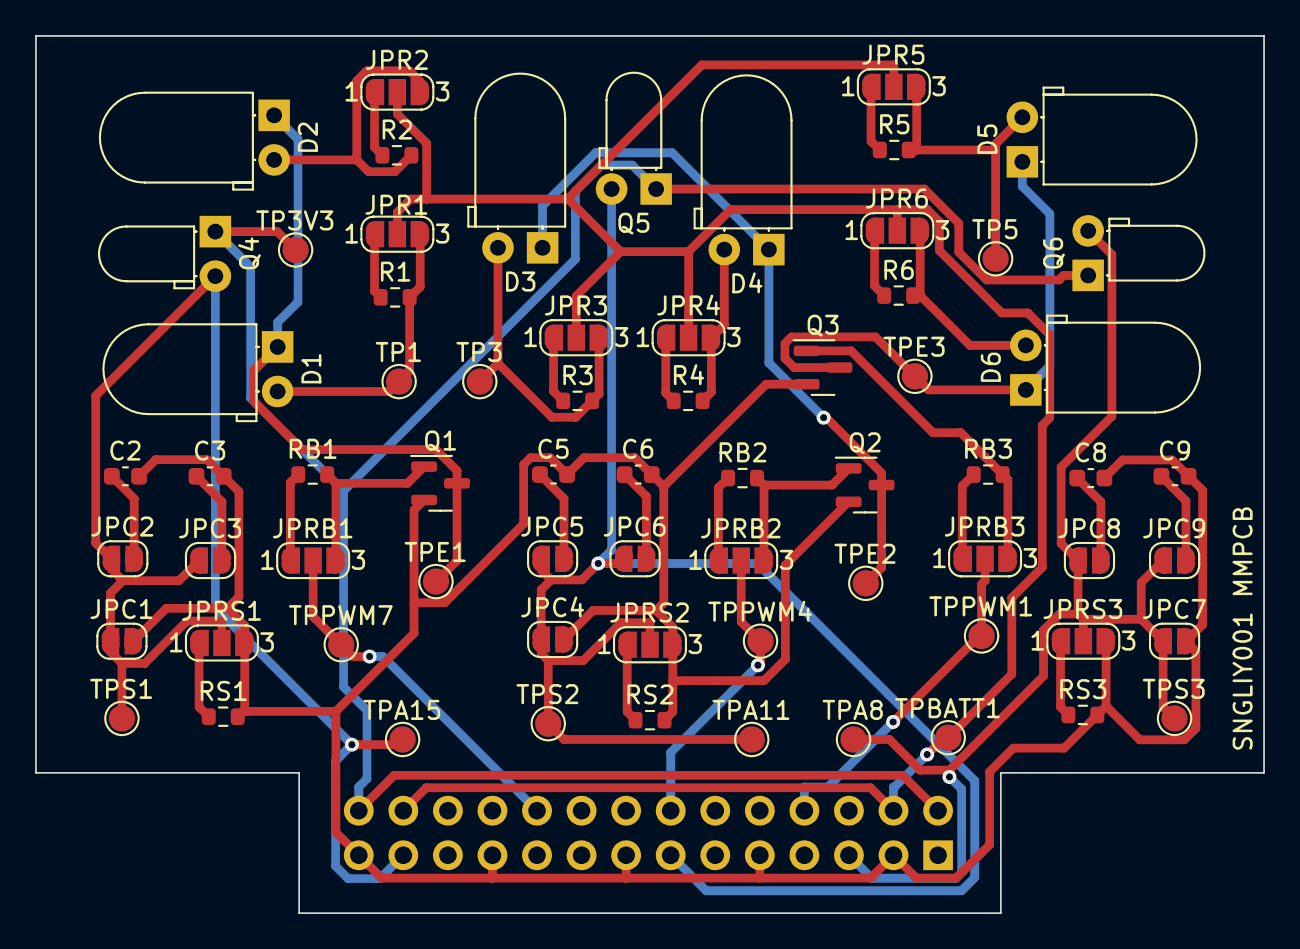
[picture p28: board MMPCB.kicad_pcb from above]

Board: 2 copper layers, 70.0 x 50.0 mm, 69 parts (1 on the bottom side), 39 nets.

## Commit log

2024-03-14 Create power_doc
2024-03-19 Update power_doc
2024-04-19 Added power-module-section-diagram.drawio
